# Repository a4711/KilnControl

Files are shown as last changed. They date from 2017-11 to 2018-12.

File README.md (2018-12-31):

# KilnControl
Control a Kiln with ESP8266.
Temperature is measured by a K-element and "MAX31855" using library from Adafruit.
Control of the device and distribution of status is done via MQTT. I am using node-red to create a front end to the device.
The heating curve can be specified by simple JSON format.

The heating wire of the kiln is controled via SSR (solid state relay). 
The kiln has to be supplied via single wire 230V. 
The SSR is behind a relay, which is connected to a safety switch (only activated if the kiln is closed).
__Dangerous: Do not connect the SSR directly between power supply and heating wire. You might have 230V on the heating wire! __

The ESP modul can be configured via WifiManager.
You have to configure your local WIFI settings, the MQTT server and the "DeviceName".
The program creates a simple web server (port 80) where you can change the "DeviceName" and the MQTT server.

The following messages are distributed via MQTT:
* status : JSON string containing multiple information: 
    "actual", "internal", "desired" and "doHeating"
    
 The program subscribes for the following messages:
 * start : the message can contain any url providing a heating curve in JSON format 
 * stop : stop the current heating process 

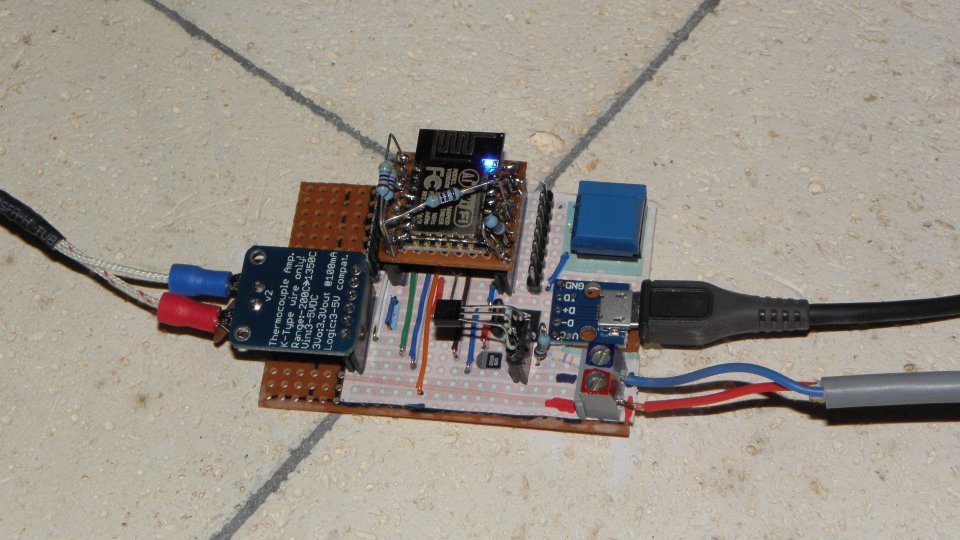
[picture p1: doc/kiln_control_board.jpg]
ESP8266 Kiln Control


Sketch
------

The micro USB connector is just for power supply. To supply the module with 3.3V a AMS1117 voltage regultor is used.
Please note, that the pins RST, EN, GPIO0 are connected to VCC with 4.7 kOhm pull-up resistors
and GPIO15 is connected to GND with 4.7 kOhm pull-down resistor directly on the ESP12F module.
You will not find them in the sketch (see photo of my board.)

The switch on the board just distributes a MQTT message but is not of any use, yet.
I added an additional temperature sensor (DS18B20) to compare it with the internal temperatur of the MAX31855.
(This additional temperature sensor is just for fun.)

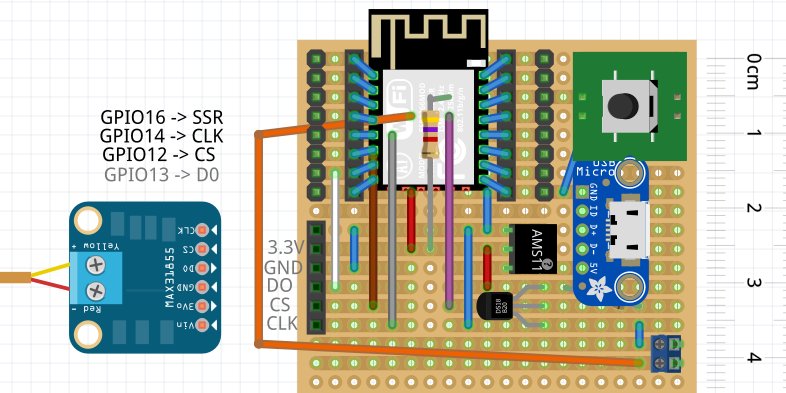
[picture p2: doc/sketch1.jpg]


Used GPIOs
----------
<table border="1">
<tr>
  <th>GPIO</th>
  <th>Function</th>
</tr>

<tr>
  <td>GPIO 0 </td>
  <td>to be pulled low for flashing (HIGH via 4.7 kOhm)</td>
</tr>

<tr>
  <td>GPIO 1</td>
  <td>Serial TX</td>
</tr>

<tr>
  <td>GPIO 2</td>
  <td>built in LED used for status blinking (HIGH via 4.7 kOhm)</td>
</tr>

<tr>
  <td>GPIO 3</td>
  <td>Serial RX</td>
</tr>

<tr>
  <td>GPIO 4</td>
  <td>Dallas Temperature Sensor DS18B20 via OneWire</td>
</tr>

<tr>
  <td>GPIO 5 </td>
  <td>Test Button : 3s -> reset, 10s -> reset + wifi reset </td>
</tr>

<tr>
  <td>GPIO 12 </td>
  <td>MAX31855 CS (SPI)</td>
</tr>

<tr>
  <td>GPIO 13 </td>
  <td>MAX31855 DO -->  MISO  (SPI)</td>
</tr>

<tr>
  <td>GPIO 14 </td>
  <td>MAX31855 Clock (SPI) </td>
</tr>

<tr>
  <td>GPIO 15</td>
  <td>-- unused -- (LOW via 4.7 kOhm)</td>
</tr>

<tr>
  <td>GPIO 16 </td>
  <td>Solid State Relay to switching mains</td>
</tr>
</table>

Heating Curve
-------------

The JSON object has to have an attribute "curve" which is an array of intervals.
Each interval has attributes: "h" (hours), "m" (minutes), "s" (seconds) and "t" (temperature).
"h", "m" and "s" specify the duration of the interval and "t" is the end temperature of the interval.
(Internally the program starts with 20°C, which is hard coded.)

Example:

    {
        "curve": [
            {
                "h": 0,
                "m": 5,
                "s": 0,
                "t": 600
            },
            {
                "h": 0,
                "m": 5,
                "s": 0,
                "t": 950
            }
        ]
    }
    
Some more pictures:
-
The kiln. On the right side you can see the thermocouple (type K) which I am using. 
Thg gray wire coming out on the top is the control side (low voltage) of the SSR.

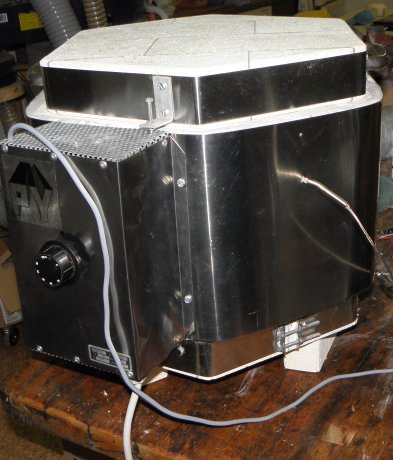
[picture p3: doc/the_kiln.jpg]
The Kiln


<hr>

Inside of the of the power control. The red thing in the upper left corner is the safety switch, which detects if the kiln is closed.
The blue thing at the bottom is the power relay, which is only active if the red switch is closed.
At the right side you see the SSR, which is controlled by the ESP8266.

The thing in the middle is a bi-metal controlling unit, which allows to set a "heating percentage". 
This unit controls the power relay (together with the safety switch). 
I don't use this unit and maybe I will replace it by another SSR, to be able to activate power remotely.

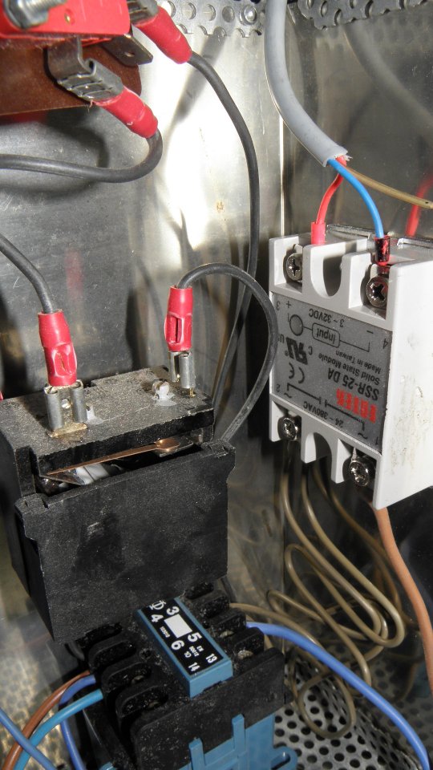
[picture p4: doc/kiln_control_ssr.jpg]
SSR after safety relay


<hr>

The thermocouple inside of the kiln.

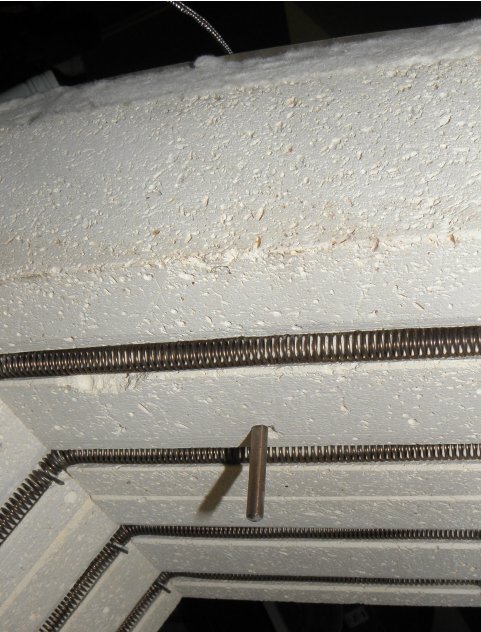
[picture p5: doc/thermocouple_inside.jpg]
Thermocouple


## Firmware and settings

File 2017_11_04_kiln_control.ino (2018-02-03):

#include <OneWire.h>
#include "myiot_DeviceConfig.h"

#include "myiot_timer_system.h"
#include "button_control.h"
#include "myiot_ota.h"
#include "led.h"
#include "TemperatureControl.h"
#include "myiot_Mqtt.h"
#include "HeatingCurve.h"
#include "myiot_webServer.h"
#include "TemperatureDistribution.h"


enum
{
  ONEWIRE = 4, // ONEWIRE bus on GPIO4
};


MyIOT::TimerSystem tsystem;
MyIOT::Mqtt mqtt;
MyIOT::DeviceConfig config;
MyIOT::OTA ota;
MyIOT::WebServer webServer;
TemperatureControl temperatureControl;
OneWire oneWire(ONEWIRE);
TemperatureDistribution ds1820(oneWire);

/*
  Ideensammlung:

    * Heizkurven über HTTP beziehen.
      MQTT "start" könnte als message die URL haben.
      -> 2017-11-04, erledigt

    * Parametrierung (config) des Device-Namens und des MQTT Servers auch anders erlauben (z.B. HTTP)
      -> 2017-11-04, erledigt mit "webServer.h"

    * Genauigkeit im MQTT "status" auf Nachkommastellen erhöhen.

    * Hardware: im Ofen das Relais mittels SSR über den ESP8266 steuern

    * Hardware: Display zur Anzeige von: aktuelle Temperature, Sollwert, Heizung (an/aus), verbleibende Zeit ...

    * Ab 800° ist das vorzeitige Bremsen unsgünstig, weil der Ofen sehr, sehr schnell abkühlt. (Vielleicht sollte man die Bremsung ab 800° einfach weg lassen.
      Mann könnte auch verschieden Korrekturen abhängig vom Temperaturbereich wählen.



*/


void setup() {
   Serial.begin(115200);

   config.setup();

   Serial.println(config.getDeviceName());
   Serial.println(config.getMqttServer());

   mqtt.setup(config.getDeviceName(), config.getMqttServer());
   std::function<void(const char* topic, const char* message)> publish = [](const char* topic, const char* message){mqtt.publish(topic,message);};

   if (!mqtt.subscribe("fire", [](const char* message) { Serial.print("fire action "); Serial.println(message); }))
   {
     Serial.println("failed to add fire subscription");
   }

   if (!mqtt.subscribe("desired", [](const char* message) { temperatureControl.update_desired( atof(message) ); }))
   {
     Serial.println("failed to add desired subscription");
   }

   if (!mqtt.subscribe("start", [](const char* message) { heatingCurve.start_curve(message);  }))
   {
     Serial.println("failed to add start subscription");
   }

   if (!mqtt.subscribe("stop", [](const char* message) { heatingCurve.stop(); Serial.println(message);}))
   {
     Serial.println("failed to add stop subscription");
   }

   webServer.setup(config);
   ota.setup(config.getDeviceName());
   blink.setup();
   buttonControl.setup(publish);
   temperatureControl.setup(publish);
   heatingCurve.setup([](const char* topic, const char* message) {temperatureControl.update_desired(atof(message)); ; Serial.println(topic); });
   ds1820.setup(publish);

   tsystem.add(&ota, MyIOT::TimerSystem::TimeSpec(0,10e6));
   tsystem.add(&webServer, MyIOT::TimerSystem::TimeSpec(0,10e6));
   tsystem.add(&blink, MyIOT::TimerSystem::TimeSpec(0,200000000));
   tsystem.add(&buttonControl, MyIOT::TimerSystem::TimeSpec(0,100000000));
   tsystem.add(&temperatureControl, MyIOT::TimerSystem::TimeSpec(5))  ;
   tsystem.add(&mqtt, MyIOT::TimerSystem::TimeSpec(0,100000000));
   tsystem.add(&heatingCurve, MyIOT::TimerSystem::TimeSpec(1));
   tsystem.add([](){ds1820.expire();}, MyIOT::TimerSystem::TimeSpec(60));
}



void loop() {
  tsystem.run_loop(10,1);
}

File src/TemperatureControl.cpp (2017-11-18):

#include <ESP8266WiFi.h>
#include "TemperatureControl.h"


TemperatureControl::TemperatureControl() :
		thermocouple(MAXCLK, MAXCS, MAXDO) {
}

void TemperatureControl::setup(
		std::function<void(const char* topic, const char* message)> fpublish) {
	publish = fpublish;
	pinMode(SSR, OUTPUT);
}

void TemperatureControl::update_desired(double newValue) {
	aging = 0;
	desired = newValue;
}

void TemperatureControl::expire() {
	bool doHeating = false;
	check_aging();
	double actual = getTemperature();
	if (isnan(actual)) {
		char msg[100];
		snprintf(msg, sizeof(msg), "Something wrong with thermocouple.");
		publish_error(msg);
		Serial.println(msg);
	} else {
		double delta = actual - previous;
		double correction = 0.0;
		if (delta > 0) {
			correction = delta * 3.5; // rising temperature
		} else {
			correction = delta * 0.5; // faling temperature
		}

#ifdef ORIGINAL_CODE
		doHeating = actual < desired;
#else
		doHeating = (actual + correction) < desired; // if temperature rises quickly, we stop heating before we reach the desired value
#endif
		if (!isDesiredValid()) doHeating = false;

		publish_actual(actual);
		publish_status(actual, getInternalTemperature(), doHeating, delta);
		aging++;
		previous = actual; // remember the last temperature
	}
	digitalWrite(SSR, doHeating ? HIGH : LOW);
}

void TemperatureControl::destroy() {
}

double TemperatureControl::getTemperature() {
	for (int i = 0; i < 5; i++) {
		double actual = thermocouple.readCelsius();
		if (isnan(actual)) {
			continue;
		}
		return actual;
	}
	return NAN;
}

double TemperatureControl::getInternalTemperature() {
	for (int i = 0; i < 5; i++) {
		double actual = thermocouple.readInternal();
		if (isnan(actual)) {
			continue;
		}
		return actual;
	}
	return NAN;
}

bool TemperatureControl::isDesiredValid() const
{
	return aging <= MAX_AGE;
}


void TemperatureControl::check_aging() {
	if (!isDesiredValid()) {
		desired = 0.0;
	}
}

void TemperatureControl::publish_actual(double actual) {
	if (!publish)
		return;

	Serial.print("C = ");
	Serial.println(actual);
	char buffer[256] = { 0 };
	int d_actual = actual;
	snprintf(buffer, sizeof(buffer), "%d", d_actual);
	publish("actual", buffer);
}

void TemperatureControl::publish_status(double actual, double internal,
		bool doHeating, double delta) {
	if (!publish)
		return;

    IPAddress localIp = WiFi.localIP();
	char buffer[1024] = { 0 };
	snprintf(buffer, sizeof(buffer),
			"{\"actual\":%d, \"internal\":%d, \"desired\":%d, \"aging\":%u, \"doHeating\":%u, \"delta\":%d, \"ip\":\"%d.%d.%d.%d\"}",
			(int) (actual), (int) (internal), (int) (desired), aging,
			(doHeating ? 1 : 0), (int) (delta),
			localIp[0],localIp[1],localIp[2],localIp[3]
	);
	publish("status", buffer);
}

void TemperatureControl::publish_error(const char* msg) {
	if (!publish)
		return;

	char buffer[256] = { 0 };
	snprintf(buffer, sizeof(buffer), "{\"error\":%s}", msg);
	publish("status", buffer);
}

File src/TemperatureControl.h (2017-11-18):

#ifndef TEMPERATURE_CONTROL_H
#define TEMPERATURE_CONTROL_H

#include <functional>
#include "Adafruit_MAX31855.h"
#include "myiot_timer_system.h"

class TemperatureControl : public MyIOT::ITimer
{
private:
  enum {
    MAXDO = 13,
    MAXCS = 12,
    MAXCLK= 14,
    SSR = 16,  // the output which controls the physical heating (solid state relay).

    MAX_AGE = 5, // if "aging" reaches MAX_AGE, the "desired" value is set to 0.0 (which will turn off heating)
  };

public:
	TemperatureControl();

	void setup(
			std::function<void(const char* topic, const char* message)> fpublish);

	void update_desired(double newValue);
  
  virtual void expire();

	virtual void destroy();

  private:
	double getTemperature();

	double getInternalTemperature();

	bool isDesiredValid() const;

	void check_aging();

	void publish_actual(double actual);
  
    void publish_status(double actual, double internal, bool doHeating,
			double delta);    

    void publish_error(const char* msg);
  
    Adafruit_MAX31855 thermocouple;
  
    unsigned int aging = MAX_AGE+1; // counter, which is incremented each cycle; when receiving a mqtt desired update, the counter is reset.
    double desired = 0.0;     // the temperature which should be reached (given my mqtt: <devicename>/desired
    double previous = 0.0;    // temperature of the previous measurement cycle

    std::function<void(const char* topic, const char* message)> publish;
    

};

#endif

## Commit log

2017-11-04 add node-red flow
2017-11-05 updated flow
2017-11-18 - added external DS18B20 temperature sensor
    timer system, now supports std::function for "expire".
    start timer control with "aged" desire value.
2017-11-18 update node-red flow
2018-01-03 little improvements for "DeviceConfig" and "webServer"
2018-01-03 add fritzing sketch to project
    [kiln_control.fzz]
2018-01-18 improved fritzing sketch
    [kiln_control.fzz]
2018-02-03 updated some components: device config, mqtt, web server
